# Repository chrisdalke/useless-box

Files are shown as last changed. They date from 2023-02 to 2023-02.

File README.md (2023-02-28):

# Useless Box

A classic Useless Machine which operates it's own "off" switch.

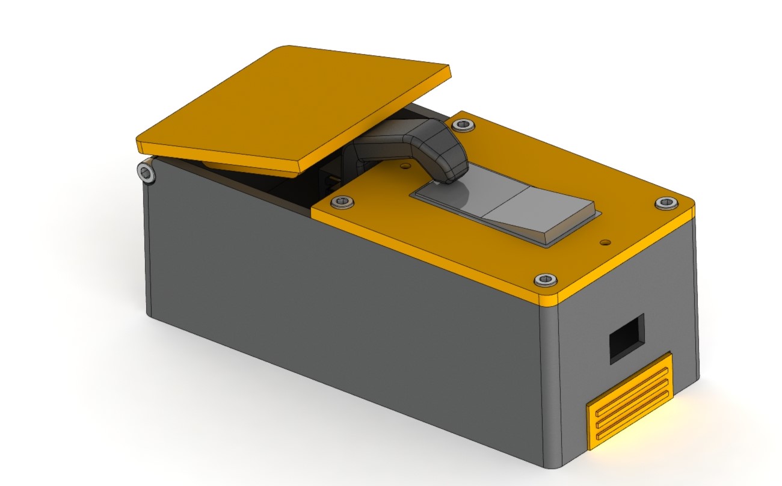
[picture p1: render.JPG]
useless box


## Overview

This repository contains the CAD, Arduino firmware, and circuit design to build the useless box featured in this video: https://www.youtube.com/watch?v=wQX75QZREI0

## Parts List

- Various 3d printed parts (in `./hardware`) printed in orange and black PLA
- Arduino Pro Micro + Breakout PCB (`./pcb`)
- Small LiPo battery
- M4 or M5 Socket Head Screw (for Hinge)

- 1x PCB ordered using Gerber files in (`./pcb`) -- 
- 1x Arduino Pro Micro
- 1x L7805CV 5V Linear Regulator
- 1x MG995 180 Degree Servo
- 1x 3-Pin JST-XH Connector (Female)
- 2x 2-Pin JST-XH Connector (Female)
- 2x 2-Pin JST-XH Connector (Male)
- 1x 2.54mm Male Pin Header

*Note: If you don't want to order a PCB, you can also build the circuit on a prototyping board yourself! Schematics in the same folder.*

TODO

## Build Instructions

1. Print all 3d-printed parts in any color/material. I used PLA, 30% infill, 0.2mm layer height.
2. Order PCB, or obtain a prototype board. (I won't go through circuit wiring instructions, check the PCB schematic in `./pcb`.)
2. Solder all components on the PCB

TODO

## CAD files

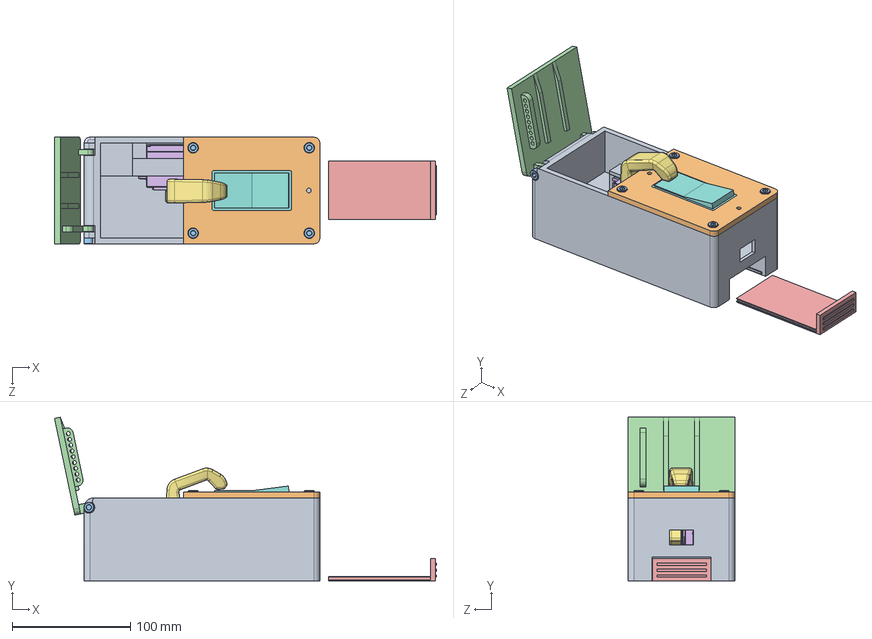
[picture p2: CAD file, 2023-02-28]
hardware/Full Assembly.SLDASM
322.4 x 138.1 x 90.0 mm
Switch Lid
91290A201_Black-Oxide Alloy Steel Socket Head Screw x 5
Moving Lid
battery lid
MG995.step
arm
switch mockup
servo hold down

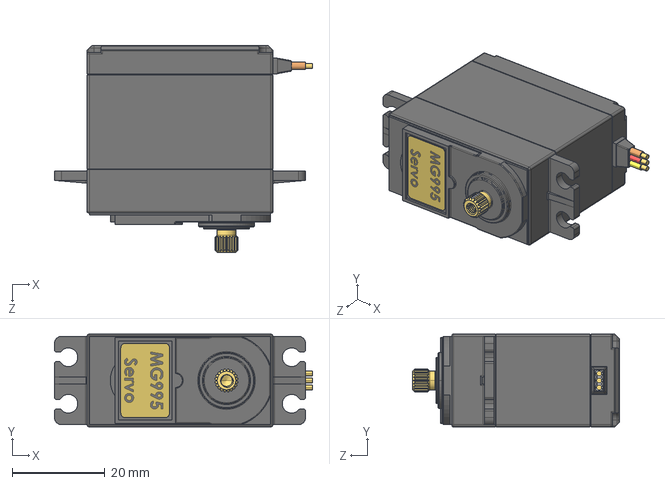
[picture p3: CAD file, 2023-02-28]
hardware/mg995-servo-motor-2.snapshot.4/MG995.STEP
55.5 x 20.0 x 44.5 mm

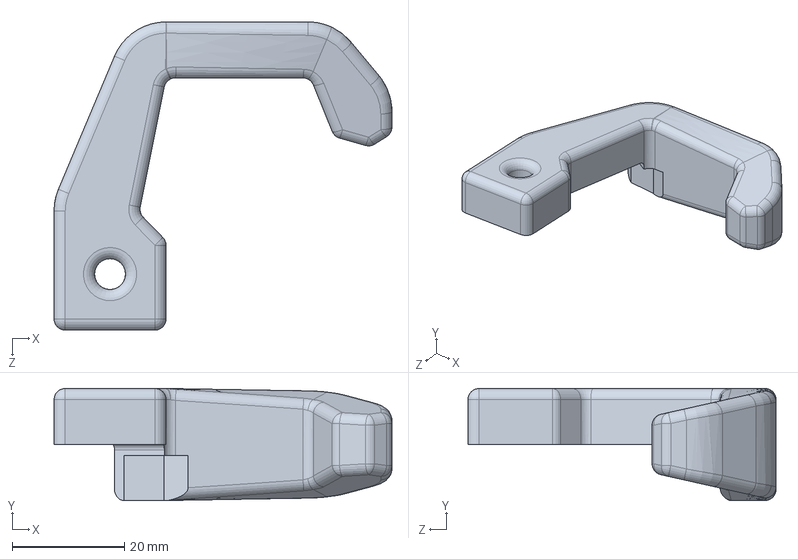
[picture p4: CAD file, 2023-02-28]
hardware/arm.SLDPRT
60.3 x 20.0 x 55.0 mm

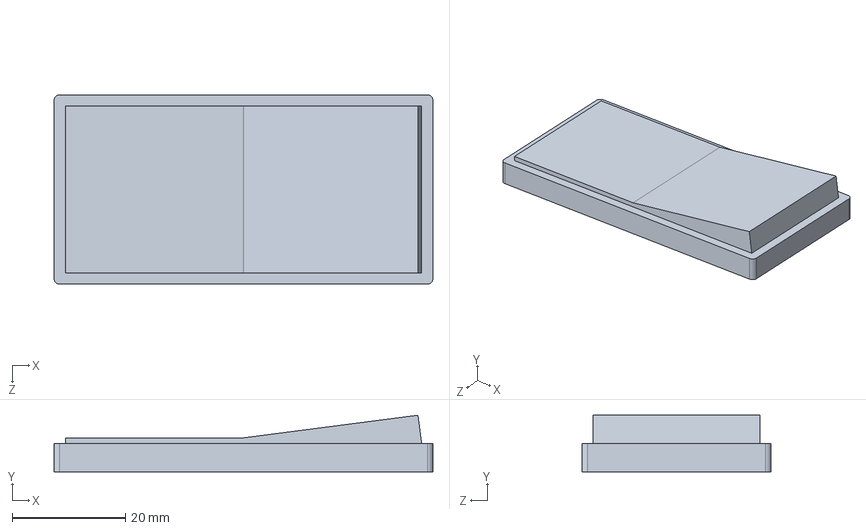
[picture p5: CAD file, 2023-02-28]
hardware/switch mockup.SLDPRT
67.0 x 10.0 x 33.5 mm

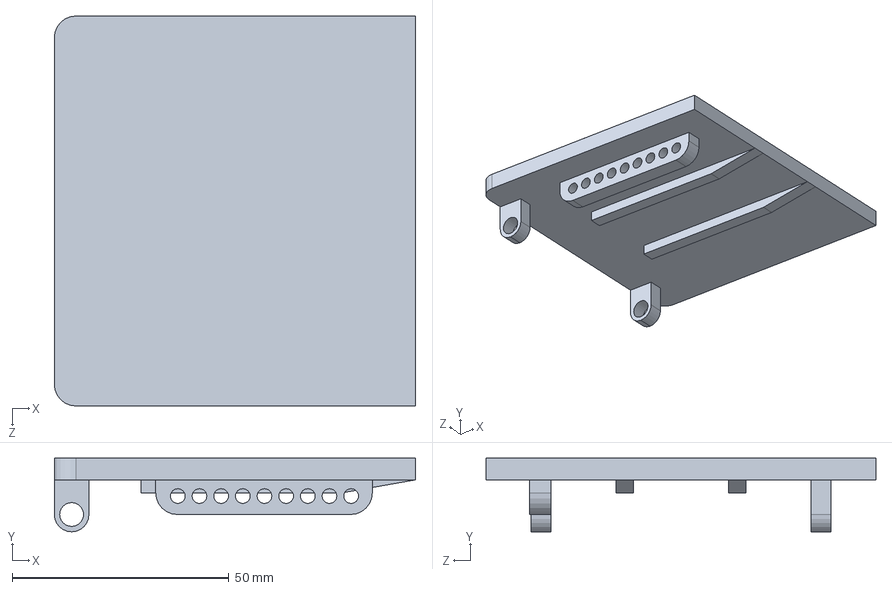
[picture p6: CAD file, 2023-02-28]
hardware/Moving Lid.SLDPRT
83.4 x 17.0 x 90.0 mm

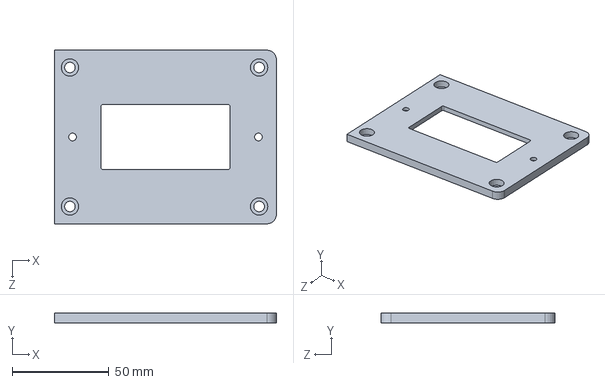
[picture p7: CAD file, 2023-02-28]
hardware/Switch Lid.SLDPRT
115.0 x 5.00 x 90.0 mm

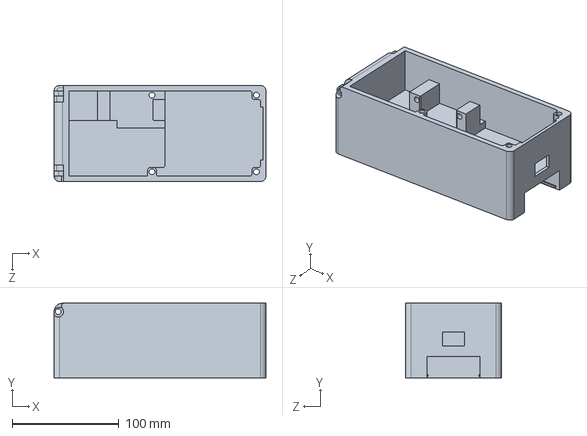
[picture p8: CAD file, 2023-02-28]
hardware/Box.SLDPRT
199.0 x 70.0 x 90.0 mm

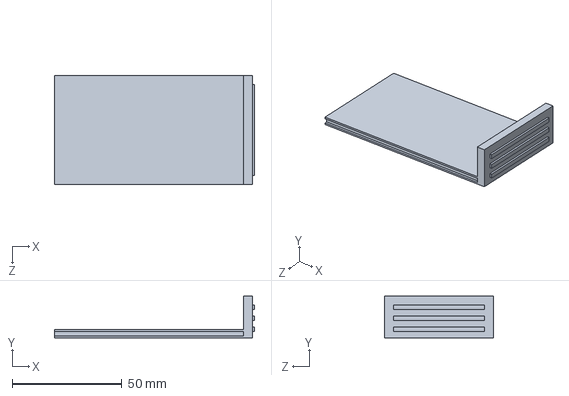
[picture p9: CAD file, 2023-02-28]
hardware/battery lid.SLDPRT
91.0 x 19.0 x 49.6 mm

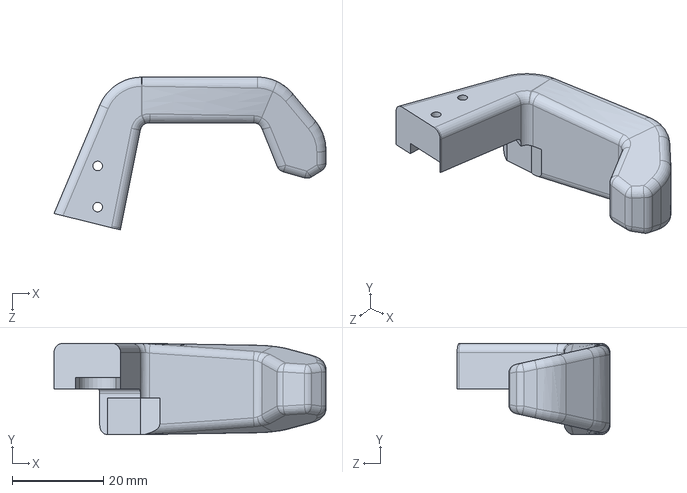
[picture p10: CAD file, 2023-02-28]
hardware/arm v2.SLDPRT
59.5 x 20.0 x 33.5 mm

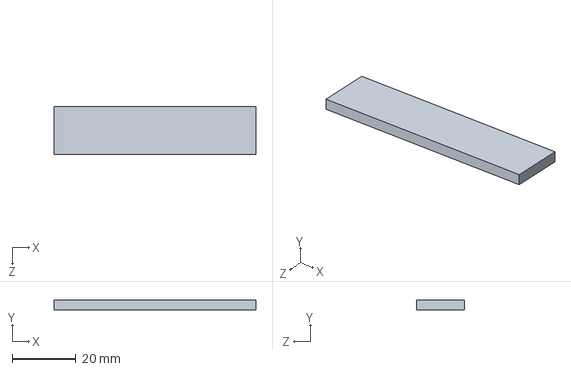
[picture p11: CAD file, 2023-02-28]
hardware/servo hold down.SLDPRT
63.3 x 3.00 x 15.0 mm

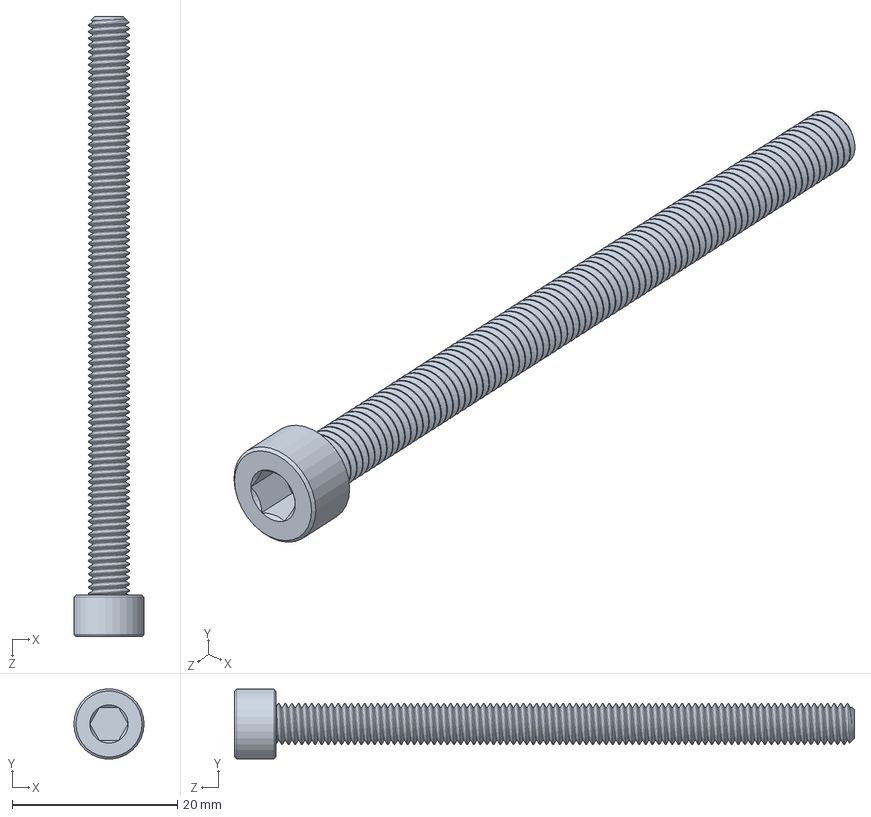
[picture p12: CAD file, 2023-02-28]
hardware/91290A201_Black-Oxide Alloy Steel Socket Head Screw.SLDPRT
8.50 x 8.45 x 75.0 mm

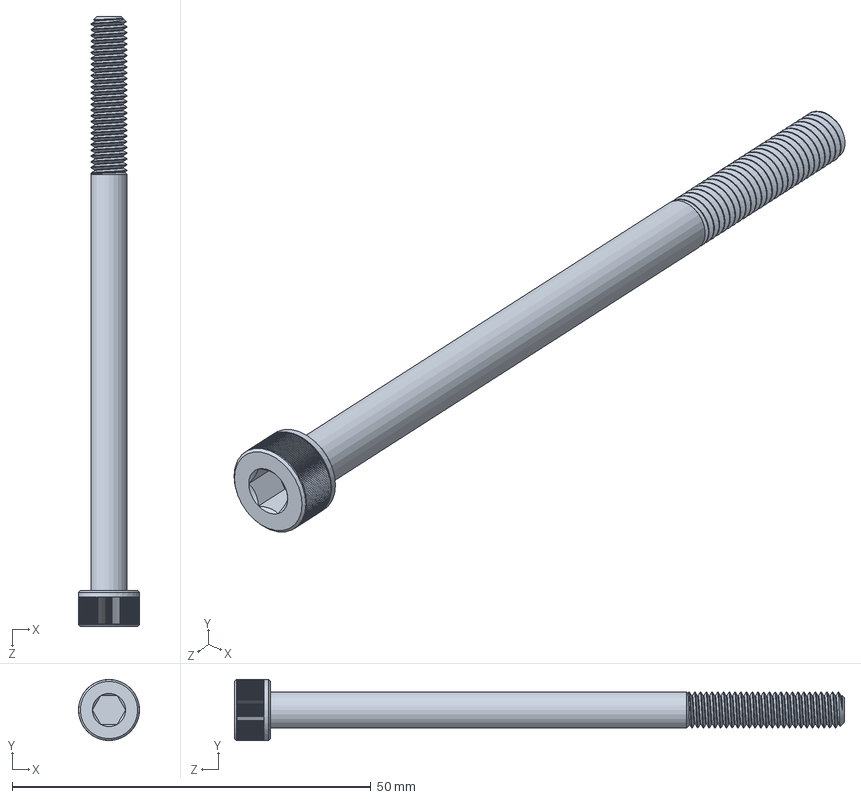
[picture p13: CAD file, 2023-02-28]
hardware/91290A276_Black-Oxide Alloy Steel Socket Head Screw.SLDPRT
8.50 x 8.50 x 85.0 mm

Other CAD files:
hardware/arm v2.STL
hardware/battery lid.STL
hardware/mg995-servo-motor-2.snapshot.4/MG995.STL

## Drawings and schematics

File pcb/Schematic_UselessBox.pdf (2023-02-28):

## Battery Input + Switch Toggle Switch

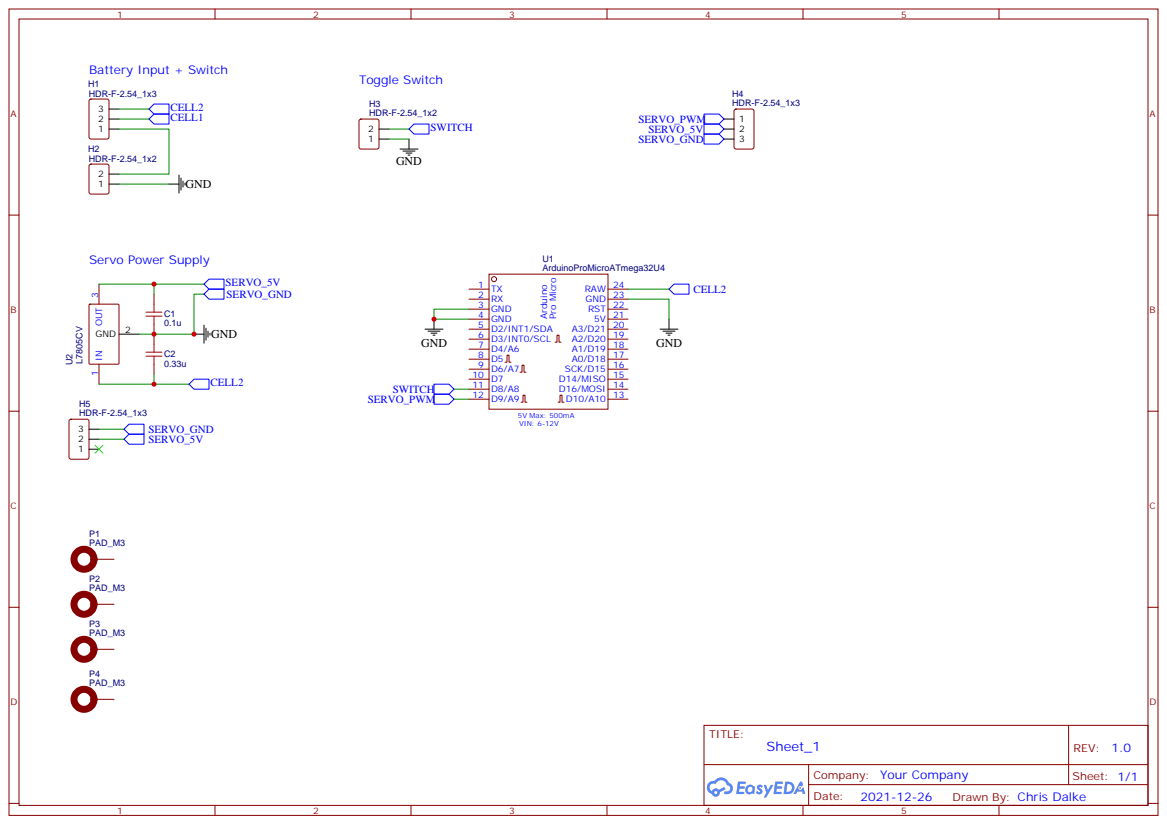
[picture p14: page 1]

Drawn By: Chris Dalke

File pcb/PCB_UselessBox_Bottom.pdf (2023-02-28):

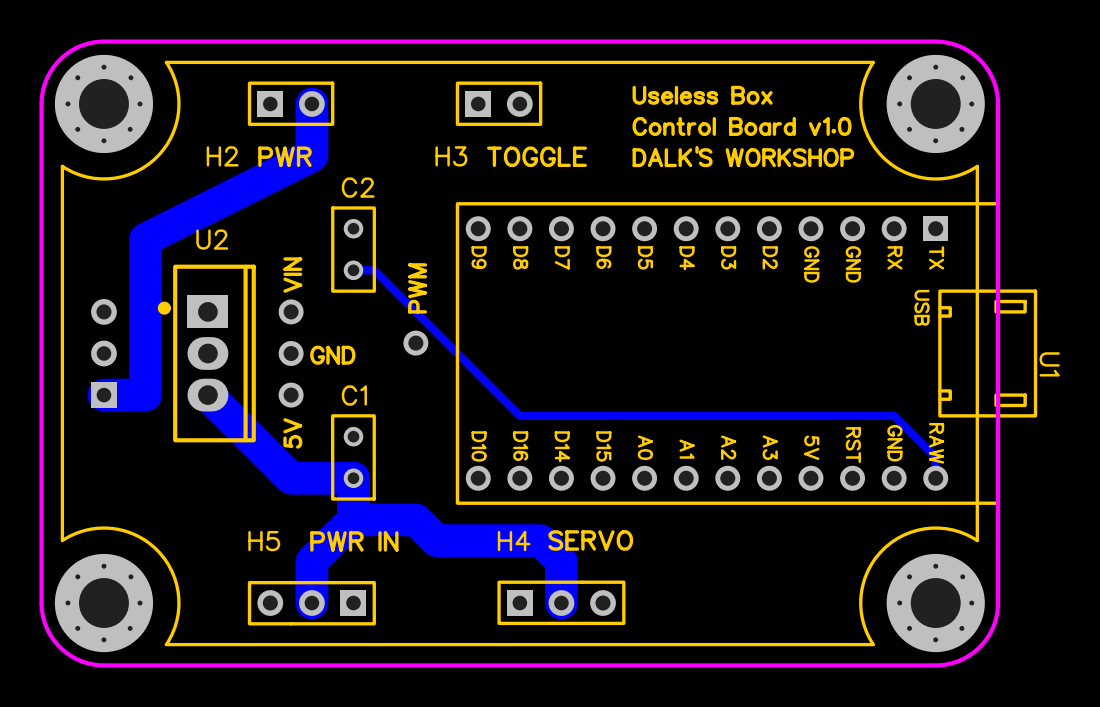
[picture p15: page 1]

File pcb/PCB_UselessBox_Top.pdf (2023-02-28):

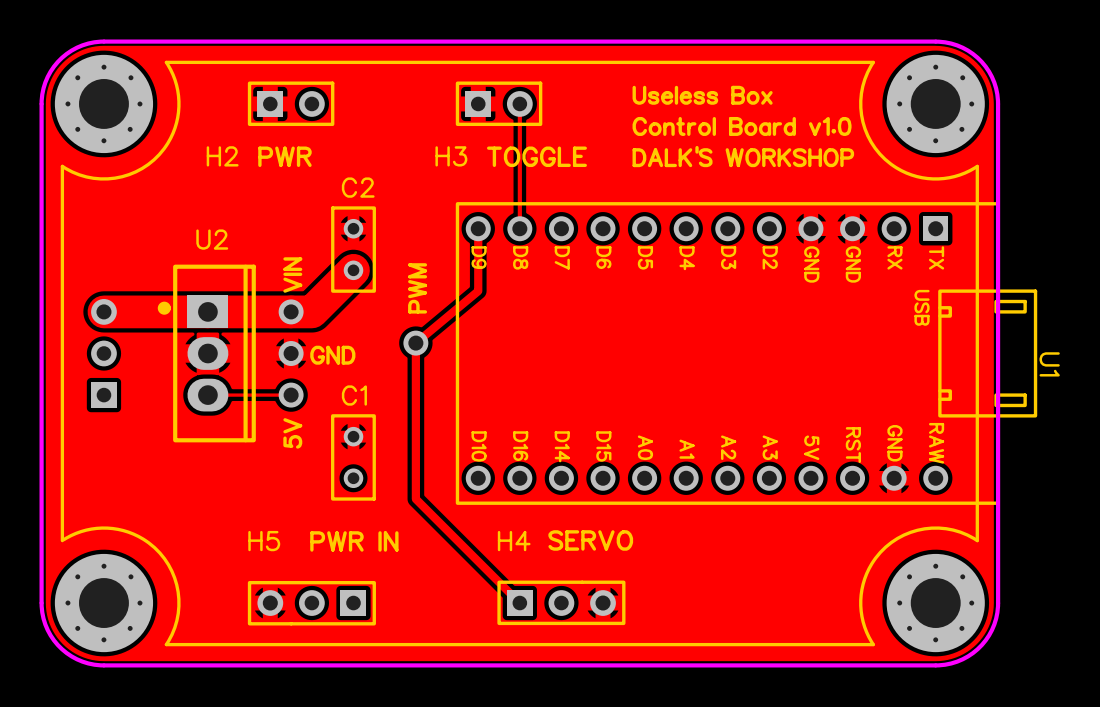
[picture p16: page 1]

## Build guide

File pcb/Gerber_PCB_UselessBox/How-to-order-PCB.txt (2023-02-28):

How to Order PCB

Please refer to:
https://docs.easyeda.com/en/PCB/Order-PCB

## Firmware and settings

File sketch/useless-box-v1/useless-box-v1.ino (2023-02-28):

#include <Servo.h>
Servo servo;

#define STATE_IDLE 0
#define STATE_EXTENDING 2
#define STATE_RESETTING 3

int extended_pos = 30;
int retracted_pos = 150;
int servo_pos = extended_pos;

int state = STATE_IDLE;
int animation_number = 0;
unsigned long resetting_cooldown_timer = 0;

// Set servo position and remember where the servo was 
void set_servo_pos(int pos) {
  servo_pos = pos;
  servo.write(pos);
}

// Sweep servo to a position with a given step size and step delay
void sweep_servo_at_speed(int target_pos, int step_size, int step_delay) {
  if (servo_pos <= target_pos) {
    for (int i = servo_pos; i <= target_pos; i += step_size) {
      servo.write(i);
      delay(step_delay);
    }
  } else {
    for (int i = servo_pos; i >= target_pos; i -= step_size) {
      servo.write(i);
      delay(step_delay);
    }
  }
  servo.write(target_pos);
  servo_pos = target_pos;
}

void setup() {
  pinMode(9, OUTPUT);
  pinMode(8, INPUT_PULLUP);
  servo.attach(9);
  Serial.begin(9600);
}

void loop() {
  bool switchVal = digitalRead(8);
  Serial.println(switchVal);

  switch (state) {
    case STATE_IDLE: {
      if (switchVal) {
        // If button is pressed, choose an animation and go into the extending state
        state = STATE_EXTENDING;
        animation_number = random(0, 5);
      }
      set_servo_pos(retracted_pos);
      break;
    }
    case STATE_EXTENDING: {
      // Execute the animation that has been randomly chosen
      switch (animation_number) {
        case 0: {
          // Normal open -> hit switch -> close
          delay(500);
          sweep_servo_at_speed(extended_pos, 3, 25);
          delay(100);
          break;
        }
        case 1: {
          // short delay after open
          delay(500);
          sweep_servo_at_speed(extended_pos, 3, 25);
          delay(500);
          break;
        }
        case 2: {
          // long delay after open
          delay(500);
          sweep_servo_at_speed(extended_pos, 3, 25);
          delay(1000);
          break;
        }
        case 3: {
          // fast 
          delay(200);
          sweep_servo_at_speed(extended_pos, 10, 30);
          delay(100);
          break;
        }
        case 4: {
          // wait a bit before starting 
          delay(4000);
          sweep_servo_at_speed(extended_pos, 3, 25);
          delay(100);
          break;
        }
      }
      state = STATE_RESETTING;
      break;
    }
    case STATE_RESETTING: {
      sweep_servo_at_speed(retracted_pos, 10, 40);
      state = STATE_IDLE;
      break;
    }
  }
  delay(10);
}

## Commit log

2023-02-28 Update files
    [91290A201_Black-Oxide Alloy Steel Socket Head Screw.SLDPRT, 91290A276_Black-Oxide Alloy Steel Socket Head Screw.SLDPRT, Box.SLDPRT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]
2023-02-28 Add PCB
    [Drill_PTH_Through.DRL, Drill_PTH_Through_Via.DRL, Gerber_BoardOutlineLayer.GKO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]
